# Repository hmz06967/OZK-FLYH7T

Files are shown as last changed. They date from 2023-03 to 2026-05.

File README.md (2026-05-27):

# OZK-FLYH7T
Eagle design witdh STM32H750x BGA flycontroller board support arduplot and betaflight tested OK but R12 no connect Vbat and can be add to boot button Just has a TP and Vbus not connected to +5V.

## Ekran Görüntüleri

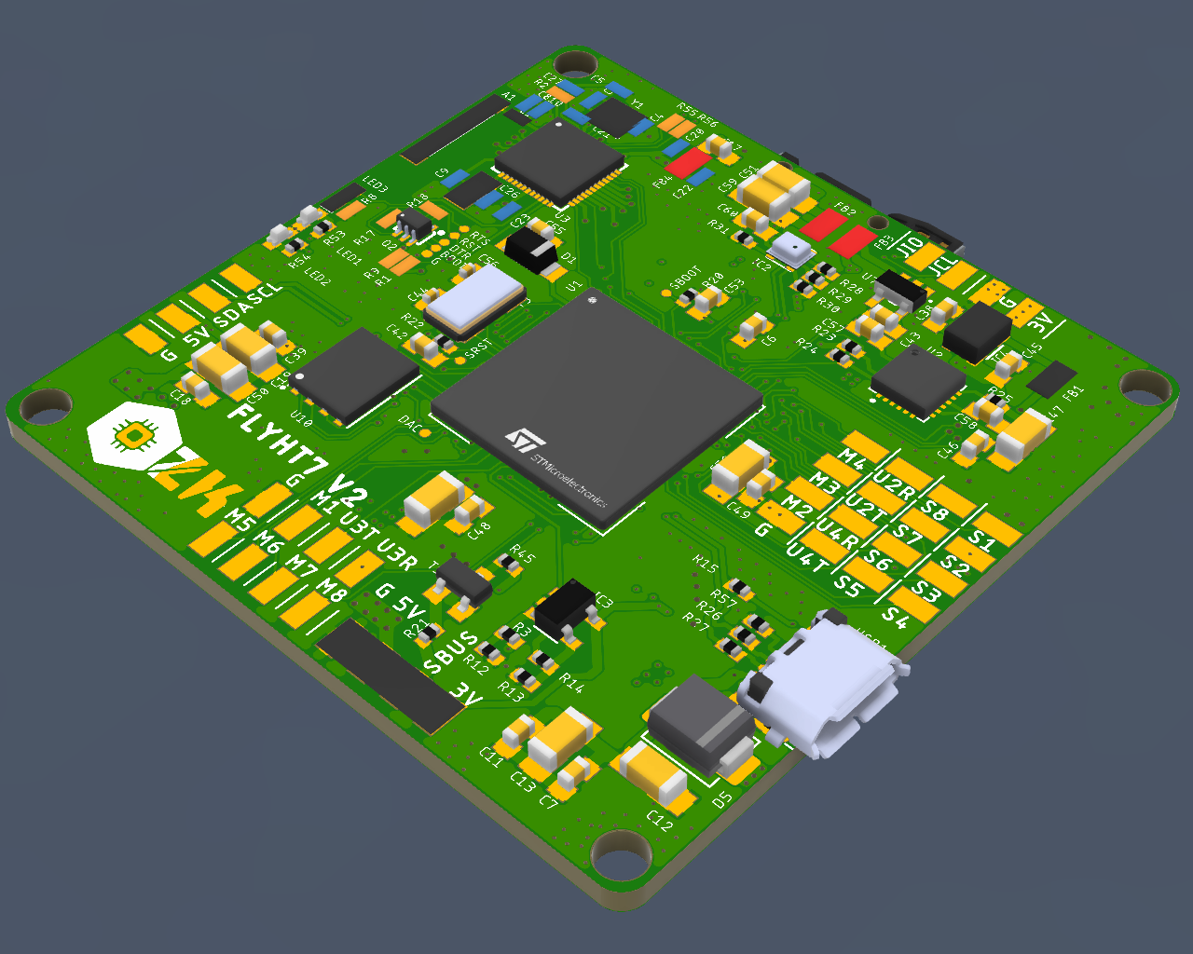
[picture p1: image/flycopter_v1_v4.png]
Uygulama Logo Görüntüsü


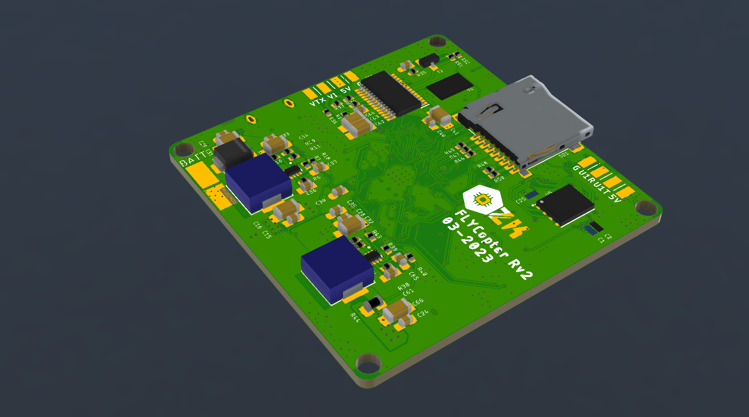
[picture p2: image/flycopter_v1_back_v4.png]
Uygulama Ekran Görüntüsü


[Canlı yazılım testi](https://www.youtube.com/watch?v=nz5CqahaaQQ)

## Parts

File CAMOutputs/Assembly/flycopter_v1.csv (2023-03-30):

Qty | Value | Device | Package | Parts | Description | ARROW_PART_NUMBER | ARROW_PRICE-STOCK | AVAILABILITY | CATEGORY | CREATED_BY | DESCRIPTION | DIGIKEY_PART_NUMBER | HEIGHT | MANUFACTURER | MANUFACTURER_NAME | MANUFACTURER_PART_NUMBER | MF | MOUSER_PART_NUMBER | MOUSER_PRICE-STOCK | MP | MPN | OPERATING_TEMP | PACKAGE | PART_STATUS | POPULARITY | PRICE | PROD_ID | PURCHASE-URL | ROHS_COMPLIANT | SERIES | SPICEPREFIX | SUB-CATEGORY | THERMALLOSS | TP_SIGNAL_NAME | TYPE | VALUE
1 |  | ANTENNA2.4GHZ-8.0X1.0MM | ANT-2.4GHZ-8.0X1.0MM | A1 | Single-ended Antennae |  |  |  |  |  |  |  |  |  |  |  |  |  |  |  |  |  |  |  |  |  | ANT-14377
1 |  | SMD5 | SMD2,54-5,08 | BATT | SMD PAD |  |  |  |  |  |  |  |  |  |  |  |  |  |  |  |  |  |  |  | 21
1 | 0 | 0OHM-0402T-1/10W | 0402-TIGHT | L1 | 0Ω resistor |  |  |  |  |  |  |  |  |  |  |  |  |  |  |  |  |  |  |  |  |  | RES-14244 |  |  |  |  |  |  |  |  | 0
2 | 0 | 10KOHM-0402T-1/16W-1% | 0402-TIGHT | R55, R56 | 10kΩ resistor |  |  |  |  |  |  |  |  |  |  |  |  |  |  |  |  |  |  |  |  |  | RES-14241 |  |  |  |  |  |  |  |  | 10k
1 | 0 | R-US_M0805 | M0805 | R44 | RESISTOR, American symbol |  |  |  |  |  |  |  |  |  |  |  |  |  |  |  |  |  |  |  | 45 |  |  |  |  |  | R
5 | 0 | R-US_R0402 | R0402 | R6, R11, R14, R38, R41 | RESISTOR, American symbol |  |  |  |  |  |  |  |  |  |  |  |  |  |  |  |  |  |  |  | 34 |  |  |  |  |  | R
4 | 0.1uF | 0.1UF-0402T-16V-10% | 0402-TIGHT | C20, C21, C23, C25 | 0.1µF ceramic capacitors |  |  |  |  |  |  |  |  |  |  |  |  |  |  |  |  |  |  |  |  |  | CAP-12416 |  |  |  |  |  |  |  |  | 0.1uF
3 | 100k | R-US_R0402 | R0402 | R10, R20, R22 | RESISTOR, American symbol |  |  |  |  |  |  |  |  |  |  |  |  |  |  |  |  |  |  |  | 34 |  |  |  |  |  | R
27 | 100nF | C-EUC0603K | C0603K | C7, C11, C14, C15, C17, C18, C24, C28, C29, C33, C35, C36, C39, C40, C42, C43, C45, C46, C48, C49, C53, C55, C57, C58, C60, C61, C64 | CAPACITOR, European symbol |  |  |  |  |  |  |  |  |  |  |  |  |  |  |  |  |  |  |  | 30 |  |  |  |  |  | C
1 | 100uF | CPOL-EUA/3216-18R | A/3216-18R | C62 | POLARIZED CAPACITOR, European symbol
1 | 10118193-0001LF | MICRO-USB-SMD-B-(10118193-0001LF) | MICRO-USB5+6P-SMD-0.65-B | USB1 | Seeed SKU 320010003 - SMD Micro USB-B |  |  |  |  |  |  |  |  |  |  |  |  |  |  |  | 10118193-0001LF |  |  |  |  |  |  |  |  |  |  |  |  |  |  | 10118193-0001LF
4 | 10k | 10KOHM-0402T-1/16W-1% | 0402-TIGHT | R1, R9, R17, R18 | 10kΩ resistor |  |  |  |  |  |  |  |  |  |  |  |  |  |  |  |  |  |  |  |  |  | RES-14241 |  |  |  |  |  |  |  |  | 10k
13 | 10k | R-US_R0402 | R0402 | R7, R32, R33, R34, R35, R39, R45, R46, R47, R48, R49, R50, R51 | RESISTOR, American symbol |  |  |  |  |  |  |  |  |  |  |  |  |  |  |  |  |  |  |  | 34 |  |  |  |  |  | R
1 | 10nF | 10NF-0402T-25V-10% | 0402-TIGHT | C5 | 0.01uF/10nF/10,000pF ceramic capacitors |  |  |  |  |  |  |  |  |  |  |  |  |  |  |  |  |  |  |  |  |  | CAP-14847 |  |  |  |  |  |  |  |  | 10nF
1 | 10nF | C-EUC0603K | C0603K | C38 | CAPACITOR, European symbol |  |  |  |  |  |  |  |  |  |  |  |  |  |  |  |  |  |  |  | 30 |  |  |  |  |  | C
1 | 10uF | 10UF-0402T-6.3V-20% | 0402-TIGHT | C22 | 10.0µF ceramic capacitors |  |  |  |  |  |  |  |  |  |  |  |  |  |  |  |  |  |  |  |  |  | CAP-14848 |  |  |  |  |  |  |  |  | 10uF
2 | 12pF | 12PF-0402T-50V-5% | 0402-TIGHT | C3, C4 | 12pF ceramic capacitors |  |  |  |  |  |  |  |  |  |  |  |  |  |  |  |  |  |  |  |  |  | CAP-14665 |  |  |  |  |  |  |  |  | 12pF
2 | 15pF | 15PF-0402T-50V-5% | 0402-TIGHT | C9, C26 | 15pF ceramic capacitors |  |  |  |  |  |  |  |  |  |  |  |  |  |  |  |  |  |  |  |  |  | CAP-13063 |  |  |  |  |  |  |  |  | 15pF
1 | 1M | R-US_R0402 | R0402 | R13 | RESISTOR, American symbol |  |  |  |  |  |  |  |  |  |  |  |  |  |  |  |  |  |  |  | 34 |  |  |  |  |  | R
11 | 1X4SMT | 1X4SMT | 1X4-SMT | CN1, CN2, CN3, CN4, CN5, CN6, CN7, CN8, CN9, CN10, CN11 | 4-pin connector
1 | 1k | 1KOHM-0402T-1/16W-1% | 0402-TIGHT | R8 | 1kΩ resistor |  |  |  |  |  |  |  |  |  |  |  |  |  |  |  |  |  |  |  |  |  | RES-14342 |  |  |  |  |  |  |  |  | 1k
1 | 1k | R-US_R0402 | R0402 | R21 | RESISTOR, American symbol |  |  |  |  |  |  |  |  |  |  |  |  |  |  |  |  |  |  |  | 34 |  |  |  |  |  | R
8 | 2.2k | R-US_R0402 | R0402 | R23, R24, R25, R28, R29, R30, R31, R52 | RESISTOR, American symbol |  |  |  |  |  |  |  |  |  |  |  |  |  |  |  |  |  |  |  | 34 |  |  |  |  |  | R
2 | 2.2uF | C-EUC0603K | C0603K | C6, C30 | CAPACITOR, European symbol |  |  |  |  |  |  |  |  |  |  |  |  |  |  |  |  |  |  |  | 30 |  |  |  |  |  | C
1 | 20k | 20KOHM-0402T-1/16W-1% | 0402-TIGHT | R2 | 20kΩ resistor |  |  |  |  |  |  |  |  |  |  |  |  |  |  |  |  |  |  |  |  |  | RES-15131 |  |  |  |  |  |  |  |  | 20k
2 | 22 | R-US_R0402 | R0402 | R26, R27 | RESISTOR, American symbol |  |  |  |  |  |  |  |  |  |  |  |  |  |  |  |  |  |  |  | 34 |  |  |  |  |  | R
2 | 22pF | C-EUC0402K | C0402K | C44, C56 | CAPACITOR, European symbol |  |  |  |  |  |  |  |  |  |  |  |  |  |  |  |  |  |  |  | 15 |  |  |  |  |  | C
1 | 22uF | CPOL-EUA/3216-18R | A/3216-18R | C63 | POLARIZED CAPACITOR, European symbol
3 | 270k | R-US_R0402 | R0402 | R3, R16, R42 | RESISTOR, American symbol |  |  |  |  |  |  |  |  |  |  |  |  |  |  |  |  |  |  |  | 34 |  |  |  |  |  | R
2 | 270pF | 270PF-0402T-50V-5% | 0402-TIGHT | C1, C2 | 270pF/0.27nF ceramic capacitors |  |  |  |  |  |  |  |  |  |  |  |  |  |  |  |  |  |  |  |  |  | CAP-15129 |  |  |  |  |  |  |  |  | 270pF
1 | 27k | R-US_R0402 | R0402 | R12 | RESISTOR, American symbol |  |  |  |  |  |  |  |  |  |  |  |  |  |  |  |  |  |  |  | 34 |  |  |  |  |  | R
1 | 3.0nF | 3.0NF-0402T-50V-5% | 0402-TIGHT | C27 | 3.0nF (3nF, 3000pF) ceramic capacitors |  |  |  |  |  |  |  |  |  |  |  |  |  |  |  |  |  |  |  |  |  | CAP-15130 |  |  |  |  |  |  |  |  | 3.0nF
1 | 3.3V | V_REG_AP2112K-3.3V | SOT23-5 | U7 | AP2112 - 600mA CMOS LDO Regulator w/ Enable |  |  |  |  |  |  |  |  |  |  |  |  |  |  |  |  |  |  |  |  |  | VREG-12457 |  |  |  |  |  |  |  |  | 3.3V
1 | 32.768kHz | CRYSTAL-32.768KHZSMD-3.2X1.5 | CRYSTAL-SMD-3.2X1.5MM | Y2 | 32.768kHz Crystal |  |  |  |  |  |  |  |  |  |  |  |  |  |  |  |  |  |  |  |  |  | XTAL-13062 |  |  |  |  |  |  |  |  | 32.768kHz
2 | 330 | R-US_R0402 | R0402 | R53, R54 | RESISTOR, American symbol |  |  |  |  |  |  |  |  |  |  |  |  |  |  |  |  |  |  |  | 34 |  |  |  |  |  | R
2 | 33nF | C-EUC0603K | C0603K | C37, C65 | CAPACITOR, European symbol |  |  |  |  |  |  |  |  |  |  |  |  |  |  |  |  |  |  |  | 30 |  |  |  |  |  | C
1 | 4.7k | R-US_R0402 | R0402 | R15 | RESISTOR, American symbol |  |  |  |  |  |  |  |  |  |  |  |  |  |  |  |  |  |  |  | 34 |  |  |  |  |  | R
1 | 4.7uH | 0630CDMCCDS-4R7MC | 0630CDMCCDS-4R7MC | U$9 | Check availability |  |  | In Stock |  |  | 4.7 µH Shielded Molded Inductor 6.3 A 33mOhm Max Nonstandard |  |  |  |  |  | Sumida |  |  | 0630CDMCCDS-4R7MC |  |  | Nonstandard Sumida |  |  | None |  | https://pricing.snapeda.com/search/part/0630CDMCCDS-4R7MC/?ref=eda
1 | 40MHz | CRYSTAL-40MHZ-SMD-2X2.5MM | CRYSTAL-SMD-2X2.5MM | Y1 | 40MHz Crystal w/ Ground Pin |  |  |  |  |  |  |  |  |  |  |  |  |  |  |  |  |  |  |  |  |  | XTAL-15127 |  |  |  |  |  |  |  |  | 40MHZ
15 | 47uF | CPOL-EUA/3216-18R | A/3216-18R | C12, C13, C16, C19, C31, C32, C34, C41, C47, C50, C51, C52, C54, C59, C66 | POLARIZED CAPACITOR, European symbol
1 | 5.11k | R-US_R0402 | R0402 | R57 | RESISTOR, American symbol |  |  |  |  |  |  |  |  |  |  |  |  |  |  |  |  |  |  |  | 34 |  |  |  |  |  | R
2 | 50k | R-US_R0402 | R0402 | R19, R43 | RESISTOR, American symbol |  |  |  |  |  |  |  |  |  |  |  |  |  |  |  |  |  |  |  | 34 |  |  |  |  |  | R
1 | 6.8uH | 0630CDMCCDS-4R7MC | 0630CDMCCDS-4R7MC | U$5 | Check availability |  |  | In Stock |  |  | 4.7 µH Shielded Molded Inductor 6.3 A 33mOhm Max Nonstandard |  |  |  |  |  | Sumida |  |  | 0630CDMCCDS-4R7MC |  |  | Nonstandard Sumida |  |  | None |  | https://pricing.snapeda.com/search/part/0630CDMCCDS-4R7MC/?ref=eda
4 | 600Ω | FERRITE_BEAD-0805-600Ω-100MHZ | 0805 | FB1, FB2, FB3, FB4 | Ferrite Bead (blocks, cores, rings, chokes, etc.) |  |  |  |  |  |  |  |  |  |  |  |  |  |  |  |  |  |  |  |  |  | NDUC-14988 |  |  |  |  |  |  |  |  | 600Ω
2 | 75 | R-US_R0402 | R0402 | R36, R37 | RESISTOR, American symbol |  |  |  |  |  |  |  |  |  |  |  |  |  |  |  |  |  |  |  | 34 |  |  |  |  |  | R
1 | 80k | R-US_R0402 | R0402 | R40 | RESISTOR, American symbol |  |  |  |  |  |  |  |  |  |  |  |  |  |  |  |  |  |  |  | 34 |  |  |  |  |  | R
1 | AT7456E | AT7456E | SOP65P640X120-29N | IC1 | Video Character Overlay Chip (OSD) |  |  |  |  |  | Video Character Overlay Chip (OSD) |  | 1.2mm |  | ICOF | AT7456E
1 | BAS16J | DIODE_DIODE-SOD123 | DIODE_SOD123 | D1 | DIODE
2 | BC817C | BC817-16-NPN-SOT23-BEC | SOT23-BEC | T1, T2 | NPN Transistror |  |  |  |  |  |  |  |  |  |  |  |  |  |  |  |  |  |  |  | 0
1 | BLUE | LED-BLUE0603 | LED-0603 | LED3 | Blue SMD LED |  |  |  |  |  |  |  |  |  |  |  |  |  |  |  |  |  |  |  |  |  | DIO-08575 |  |  |  |  |  |  |  |  | BLUE
1 | BMP280 | BMP280 | BMP280 | IC2 | BOSCH BMP280 Digital Pressure Sensor
2 | DNP | CAP-0402-TIGHT | 0402-TIGHT | C8, C10
2 | ECS-240-12-30BQ-AEN-TR | ECS-240-12-30BQ-AEN-TR | XTAL_ECS-240-12-30BQ-AEN-TR | Y3, Y4 | The ECX-53BQ is a miniature SMD Crystal with a 3.2 x 5 mm |  |  | In Stock |  |  | 24 MHz ±25ppm Crystal 12pF 30 Ohms 4-SMD, No Lead |  |  |  |  |  | ECS Inc. |  |  | ECS-240-12-30BQ-AEN-TR |  |  | SMD-4 ECS International |  |  | None |  | https://pricing.snapeda.com/search/part/ECS-240-12-30BQ-AEN-TR/?ref=eda
1 | ESP32 | ESP32 | QFN48-0.4MM | U3 | Espressif ESP32 |  |  |  |  |  |  |  |  |  |  |  |  |  |  |  |  |  |  |  |  |  | IC-13338
1 | LD398518RG | LD398518RG | TSOT23-5L | IC4 | Ultra low drop and low noise BiCMOS voltage regulators |  |  |  |  |  |  |  |  |  |  |  |  |  |  |  |  |  |  |  | 0
1 | MBT3904DW1T1 | TRANS_NPN_DUAL-MBT3904DW1T1 | SC70-6 | Q2 | Dual NPN Transistors in Single Package |  |  |  |  |  |  |  |  |  |  |  |  |  |  |  |  |  |  |  |  |  | TRANS-13337
1 | MCP6001T_SOT23 | MCP6001T_SOT23 | SOT95P280X145-5N | IC3 | Low-Power Operational Amplifier |  |  |  | Amplifier |  | Low-Power Operational Amplifier |  |  | Microchip Technology |  |  |  |  |  |  | Generic |  |  |  |  |  |  |  |  | MCP6001 |  | OpAmp
1 | MPU-6050 | MPU-6050 | 24-VFQFN | U2 | IMU ACCEL/GYRO 3-AXIS I2C 24QFN |  |  |  |  | PCBLayout.com |  | 1428-1007-1-ND |  | TDK InvenSense |  |  |  |  |  |  | MPU-6050 |  | 24-VFQFN
2 | SS54B | SS54B | SMB | D3, D5 | SURFACE MOUNT SCHOTTKY BARRIER RECTIFIERS |  |  |  |  | PCBLayout.com |  |  |  | JCET |  |  |  |  |  |  | SS54B |  | SMB
1 | STM32H750XBH6 | STM32H750XBH6 | IC_STM32H750XBH6 | U1 | Check availability |  |  | In Stock |  |  | ARM® Cortex®-M7 STM32H7 Microcontroller IC 32-Bit Single-Core 480MHz 128KB (128K x 8) FLASH 240+25-TFBGA (14x14) |  |  |  |  |  | STMicroelectronics |  |  | STM32H750XBH6 |  |  | TFBGA-265 STMicroelectronics |  |  | None |  | https://pricing.snapeda.com/search/part/STM32H750XBH6/?ref=eda
1 | TF-HOLDER | TF-HOLDER | TF-PULL | SD1 | TF / Micro SD socket is PUSH-PUSH type, the card can be pushed into and auto locked and pushed out by simply press the card.
2 | TPS62933PDRLR | TPS62933PDRLR | SOFL50P160X60-8N | U4, U6 | Check availability |  |  | In Stock |  |  | Buck Switching Regulator IC Positive Adjustable 0.8V 1 Output 3A SOT-583 |  |  |  |  |  | Texas Instruments |  |  | TPS62933PDRLR |  |  | None |  |  | None |  | https://pricing.snapeda.com/search/part/TPS62933PDRLR/?ref=eda
8 | TPTP06R | TPTP06R | TP06R | BOOT, DAC, DTR, G, RST, RTS, SBOOT, SRST | Test pad
2 | W25QXX128MBIT-6X5-SKINNY_CENTER | W25QXX128MBIT-6X5-SKINNY_CENTER | WSON-8-6X5-SKINNY_CENTERPAD | U5, U10 |  |  |  |  |  |  |  |  |  |  |  |  |  |  |  |  |  |  |  |  |  |  | IC-15107
1 | blue | LEDCHIPLED_0603 | CHIPLED_0603 | LED1 | LED
1 | green | LEDCHIPLED_0603 | CHIPLED_0603 | LED2 | LED

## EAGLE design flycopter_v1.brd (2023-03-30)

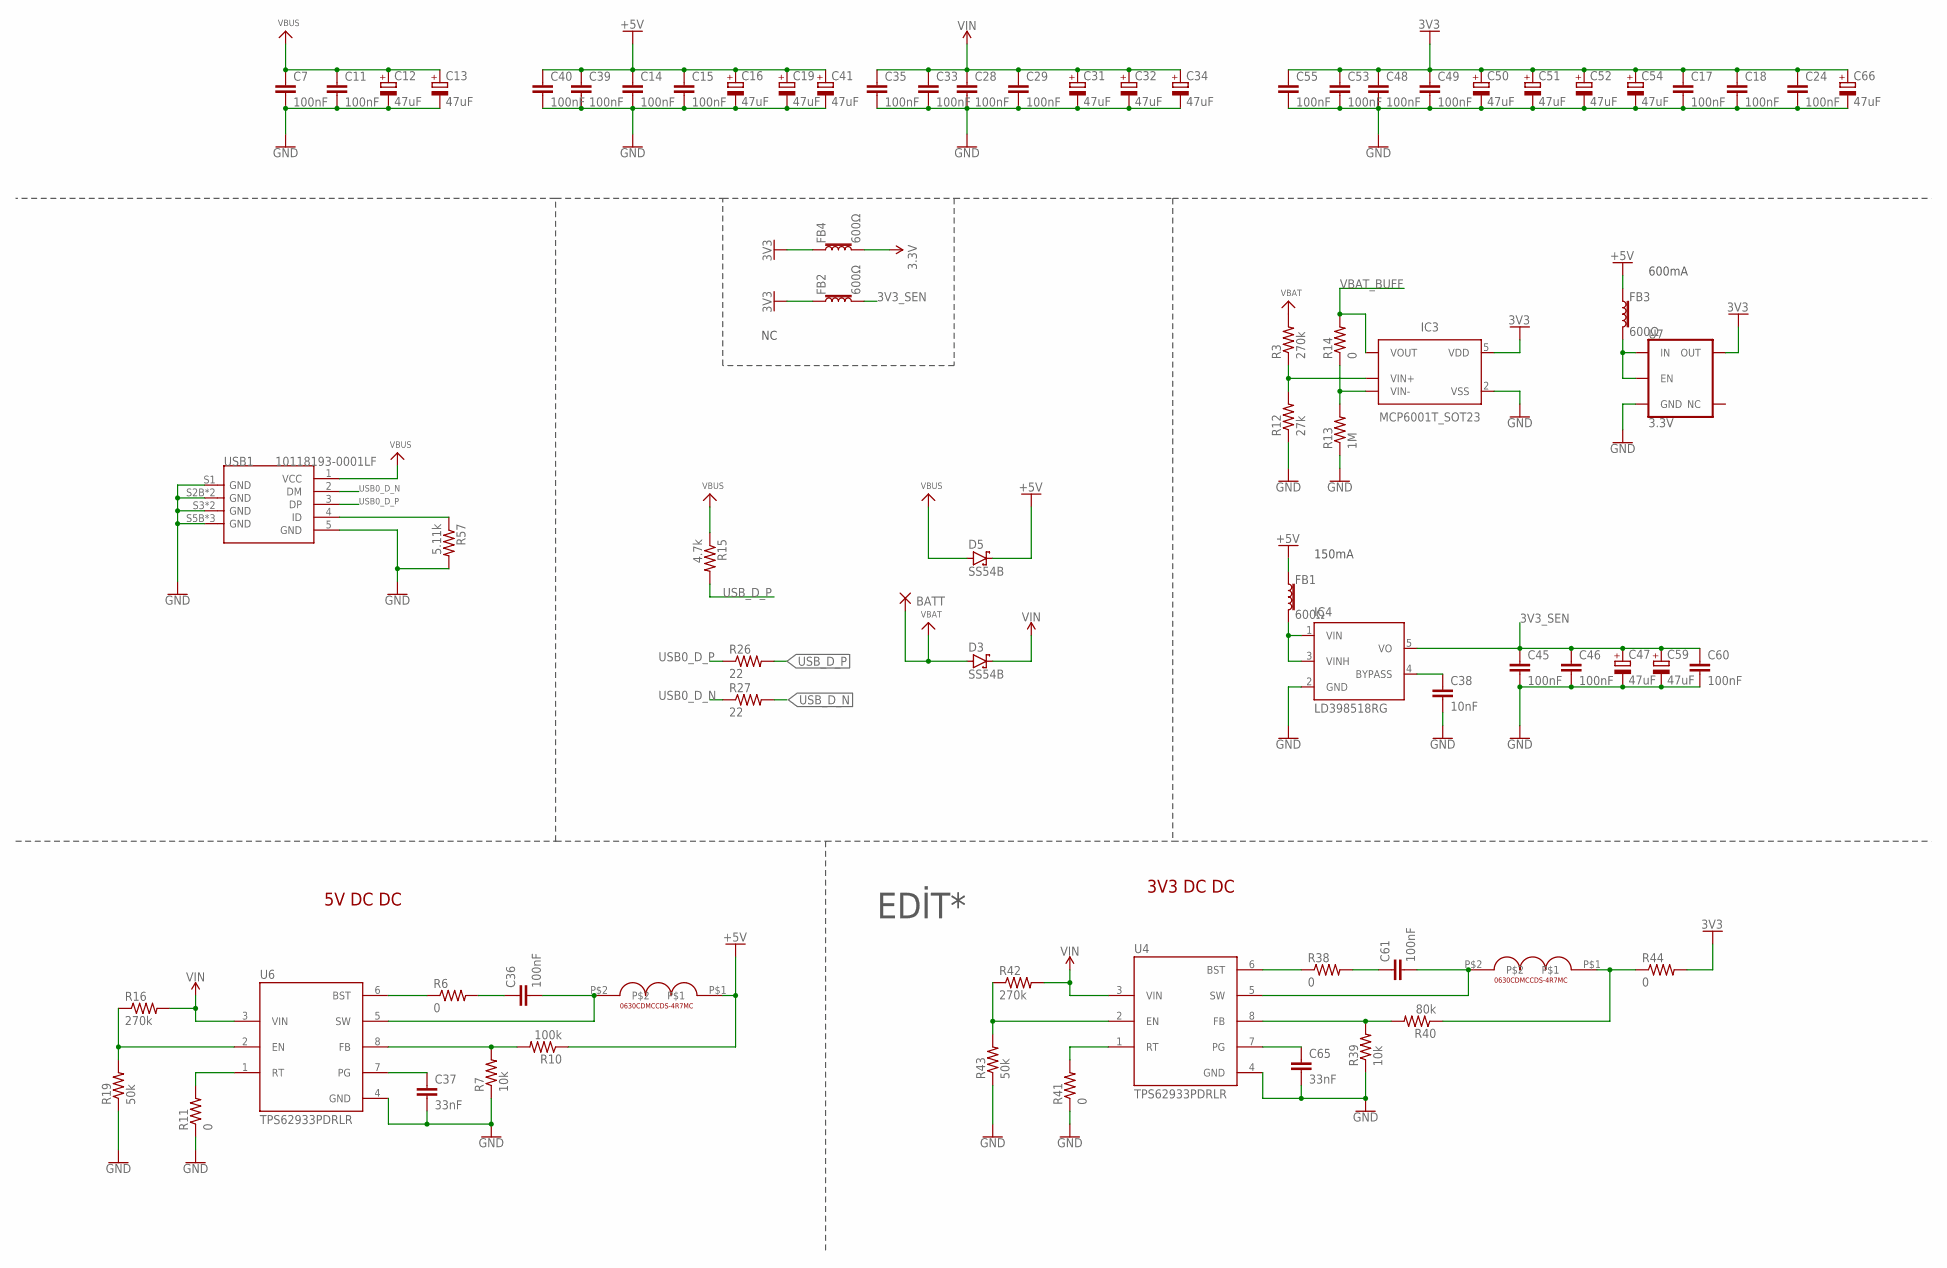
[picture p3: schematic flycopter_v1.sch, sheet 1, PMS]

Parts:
BATT: SMD5; SMD2,54-5,08
C7, C11, C14, C15, C17, C18, C24, C28, C29, C33, C35, C36, C39, C40, C45, C46, C48, C49, C53, C55, C60, C61: 100nF; C0603K
C12, C13, C16, C19, C31, C32, C34, C41, C47, C50, C51, C52, C54, C59, C66: 47uF; A/3216-18R
C37, C65: 33nF; C0603K
C38: 10nF; C0603K
D3, D5: SS54B; SMB
FB1, FB2, FB3, FB4: 600Ω; 0805
IC3: MCP6001T_SOT23; SOT95P280X145-5N
IC4: LD398518RG; TSOT23-5L
R3, R16, R42: 270k; R0402
R6, R11, R14, R38, R41: 0; R0402
R7, R39: 10k; R0402
R10: 100k; R0402
R12: 27k; R0402
R13: 1M; R0402
R15: 4.7k; R0402
R19, R43: 50k; R0402
R26, R27: 22; R0402
R40: 80k; R0402
R44: 0; M0805
R57: 5.11k; R0402
U4, U6: TPS62933PDRLR; SOFL50P160X60-8N
U7: 3.3V; SOT23-5
U$5: 6.8uH; 0630CDMCCDS-4R7MC
U$9: 4.7uH; 0630CDMCCDS-4R7MC
USB1: 10118193-0001LF; MICRO-USB5+6P-SMD-0.65-B

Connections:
3.3V: FB4.2; also elsewhere on the board
3V3: C17.1, C18.1, C24.1, C48.1, C49.1, C50.+, C51.+, C52.+, C53.1, C54.+, C55.1, C66.+, FB2.1, FB4.1, IC3.5 (VDD), R44.2, U7.5 (OUT); also elsewhere on the board
3V3_SEN: C45.1, C46.1, C47.+, C59.+, C60.1, FB2.2, IC4.5 (VO); also elsewhere on the board
+5V: C14.1, C15.1, C16.+, C19.+, C39.1, C40.1, C41.+, D5.C, FB1.1, FB3.1, R10.1, U$5.P$1; also elsewhere on the board
GND: C7.2, C11.2, C12.-, C13.-, C14.2, C15.2, C16.-, C17.2, C18.2, C19.-, C24.2, C28.2, C29.2, C31.-, C32.-, C33.2, C34.-, C35.2, C37.2, C38.2, C39.2, C40.2, C41.-, C45.2, C46.2, C47.-, C48.2, C49.2, C50.-, C51.-, C52.-, C53.2, C54.-, C55.2, C59.-, C60.2, C65.2, C66.-, IC3.2 (VSS), IC4.2 (GND), R7.1, R11.1, R12.1, R13.1, R19.1, R39.1, R41.1, R43.1, R57.2, U4.4 (GND), U6.4 (GND), U7.2 (GND), USB1.5 (GND), USB1.S1 (GND), USB1.S2B (GND), USB1.S2T (GND), USB1.S3 (GND), USB1.S4 (GND), USB1.S5B (GND), USB1.S5T (GND), USB1.S6 (GND); also elsewhere on the board
unnamed: C36.2, U6.5 (SW), U$5.P$2
unnamed: C36.1, R6.2
unnamed: R6.1, U6.6 (BST)
unnamed: R7.2, R10.2, U6.8 (FB)
unnamed: C37.1, U6.7 (PG)
unnamed: R16.1, R19.2, U6.2 (EN)
unnamed: R11.2, U6.1 (RT)
unnamed: FB1.2, IC4.1 (VIN), IC4.3 (VINH)
unnamed: C38.1, IC4.4 (BYPASS)
unnamed: FB3.2, U7.1 (IN), U7.3 (EN)
unnamed: IC3.4 (VIN-), R13.2, R14.1
unnamed: IC3.3 (VIN+), R3.1, R12.2
unnamed: C61.2, U4.5 (SW), U$9.P$2
unnamed: R57.1, USB1.4 (ID)
unnamed: C61.1, R38.2
unnamed: R38.1, U4.6 (BST)
unnamed: R39.2, R40.2, U4.8 (FB)
unnamed: C65.1, U4.7 (PG)
unnamed: R41.2, U4.1 (RT)
unnamed: R42.1, R43.2, U4.2 (EN)
unnamed: R40.1, R44.1, U$9.P$1
USB0_D_N: R27.1, USB1.2 (DM)
USB0_D_P: R26.1, USB1.3 (DP)
USB_D_N: R27.2; also elsewhere on the board
USB_D_P: R15.2, R26.2; also elsewhere on the board
VBAT: BATT.1, D3.A, R3.2
VBAT_BUFF: IC3.1 (VOUT), R14.2; also elsewhere on the board
VBUS: C7.1, C11.1, C12.+, C13.+, D5.A, R15.1, USB1.1 (VCC)
VIN: C28.1, C29.1, C31.+, C32.+, C33.1, C34.+, C35.1, D3.C, R16.2, R42.2, U4.3 (VIN), U6.3 (VIN)

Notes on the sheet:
150mA
600mA
EDİT*
5V DC DC
3V3 DC DC

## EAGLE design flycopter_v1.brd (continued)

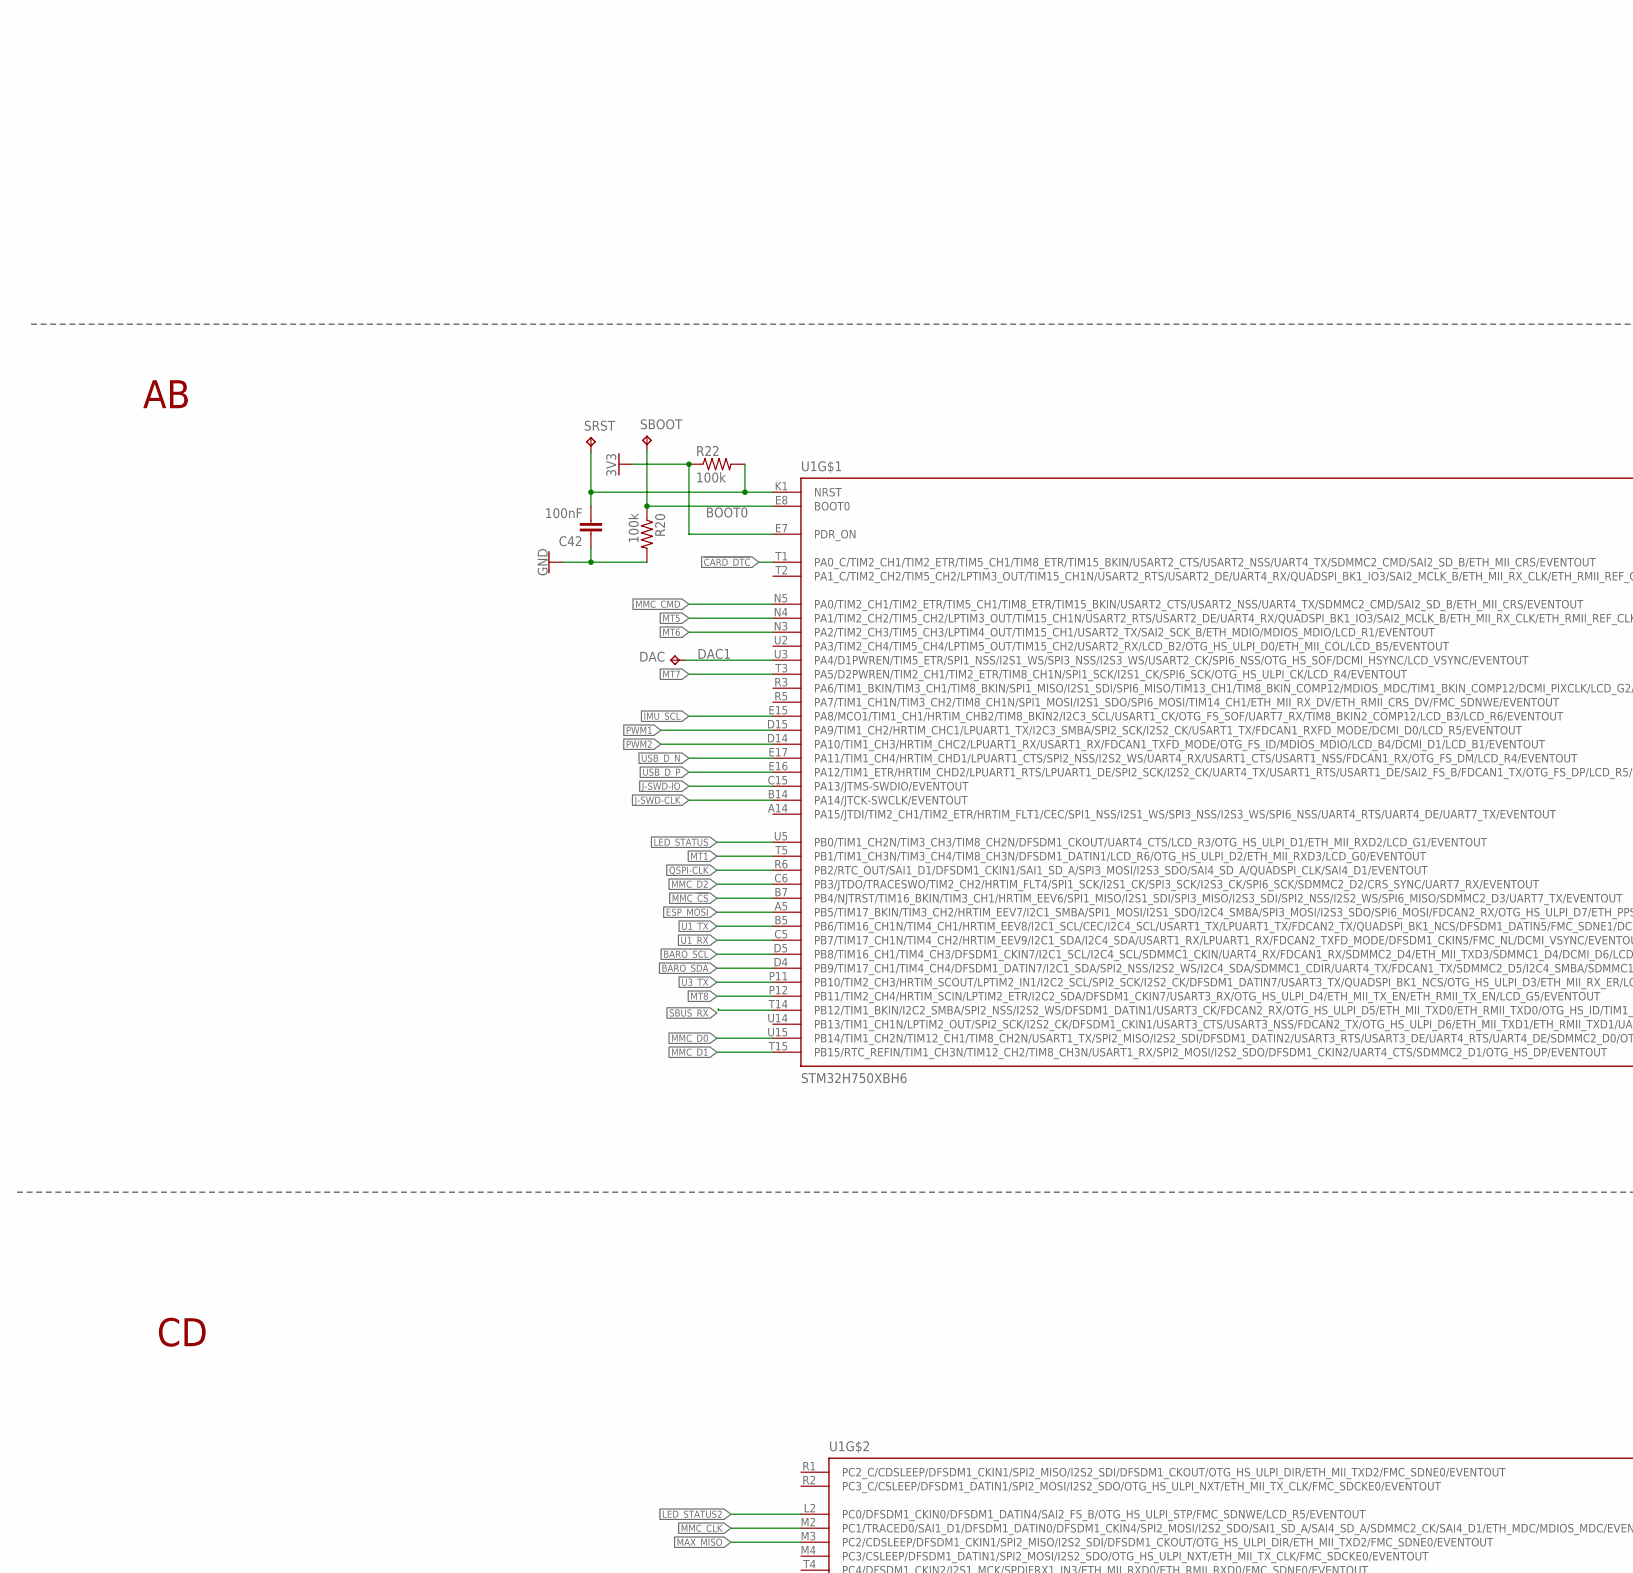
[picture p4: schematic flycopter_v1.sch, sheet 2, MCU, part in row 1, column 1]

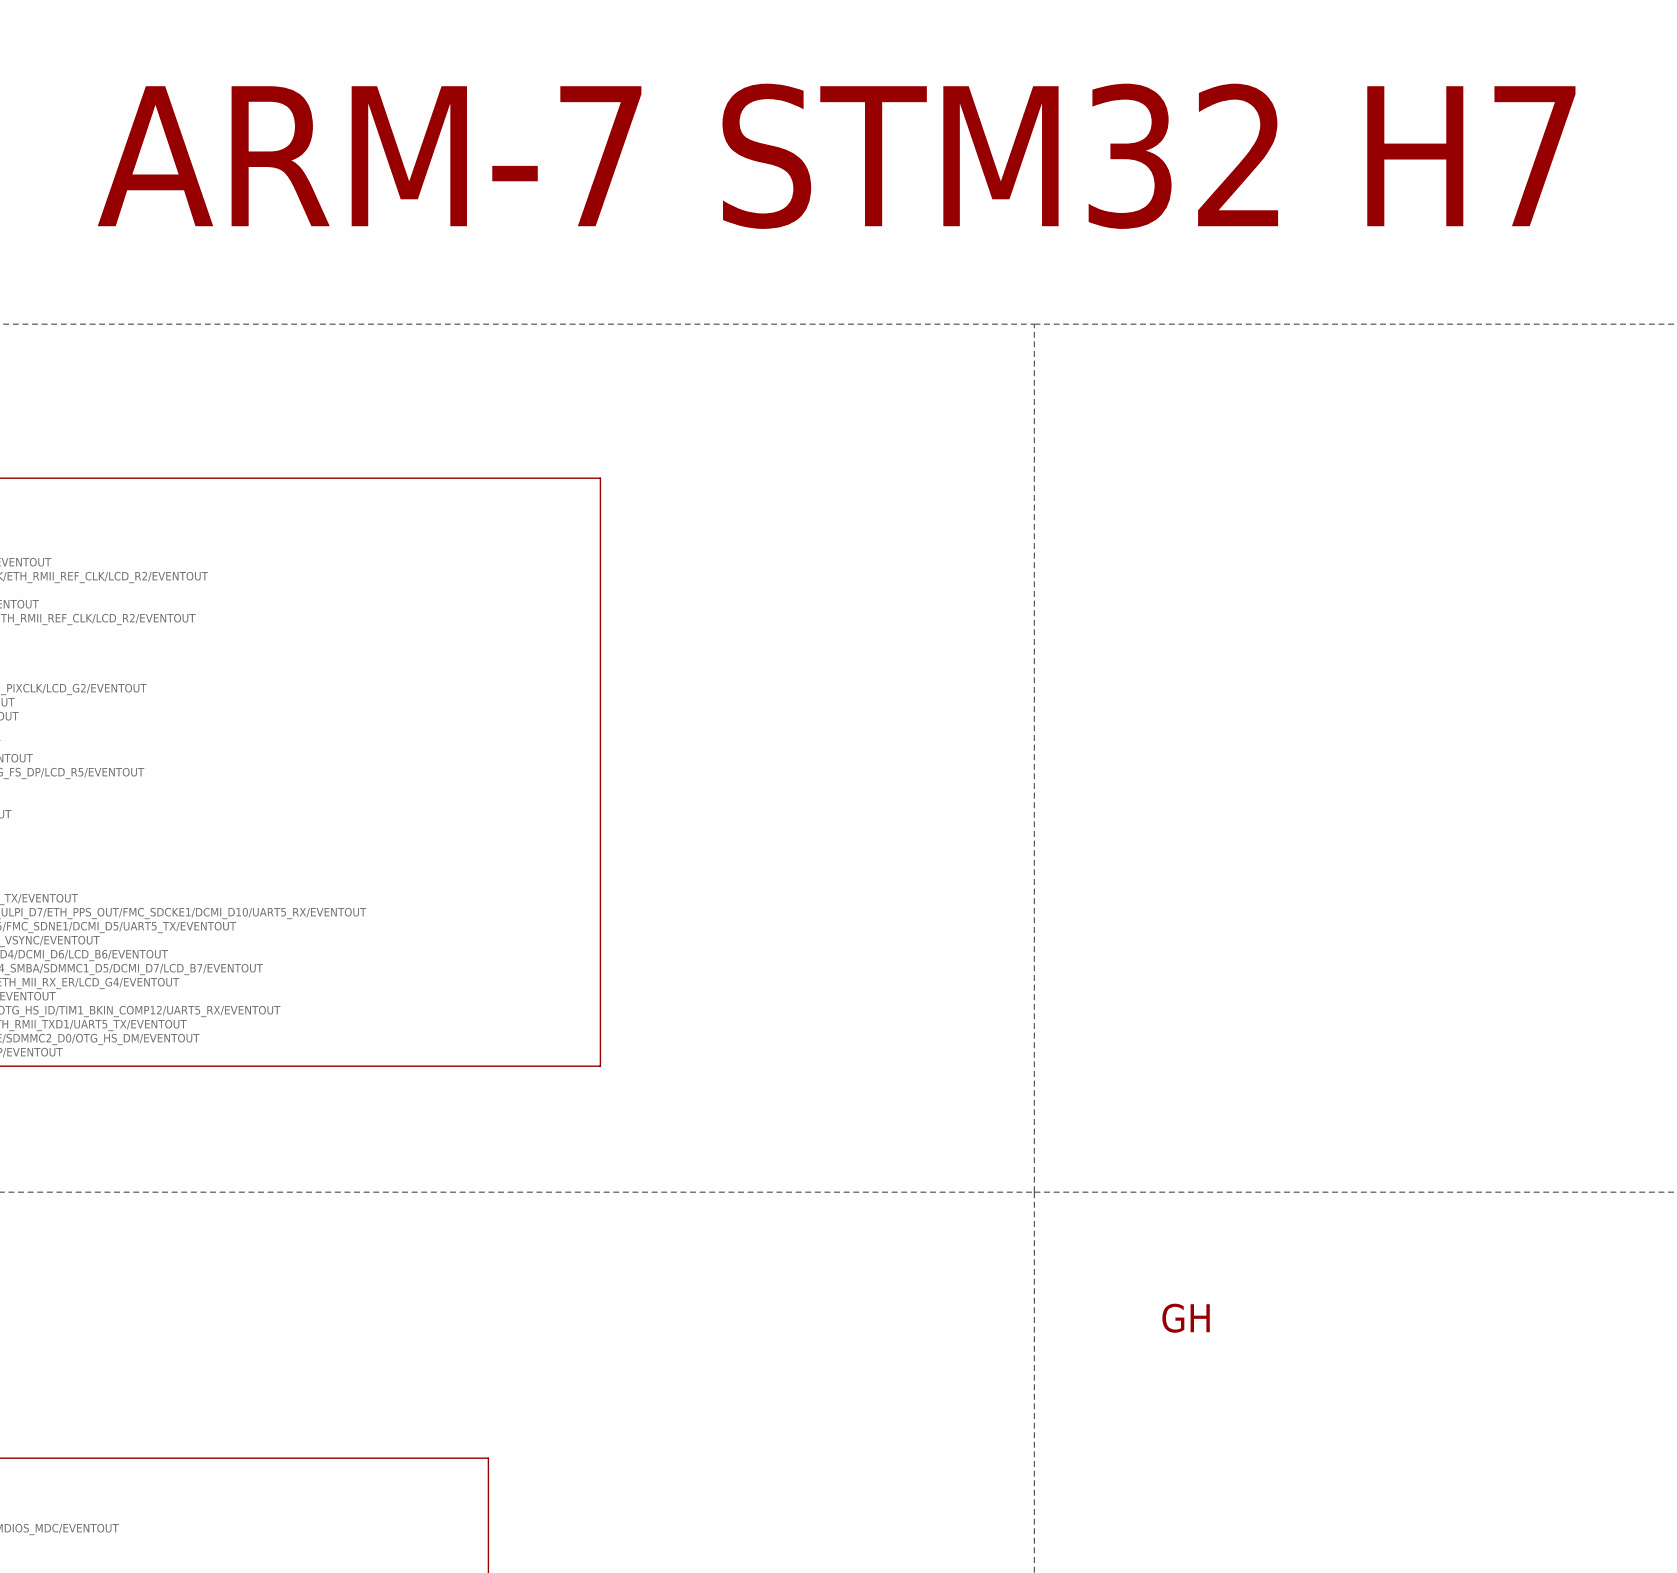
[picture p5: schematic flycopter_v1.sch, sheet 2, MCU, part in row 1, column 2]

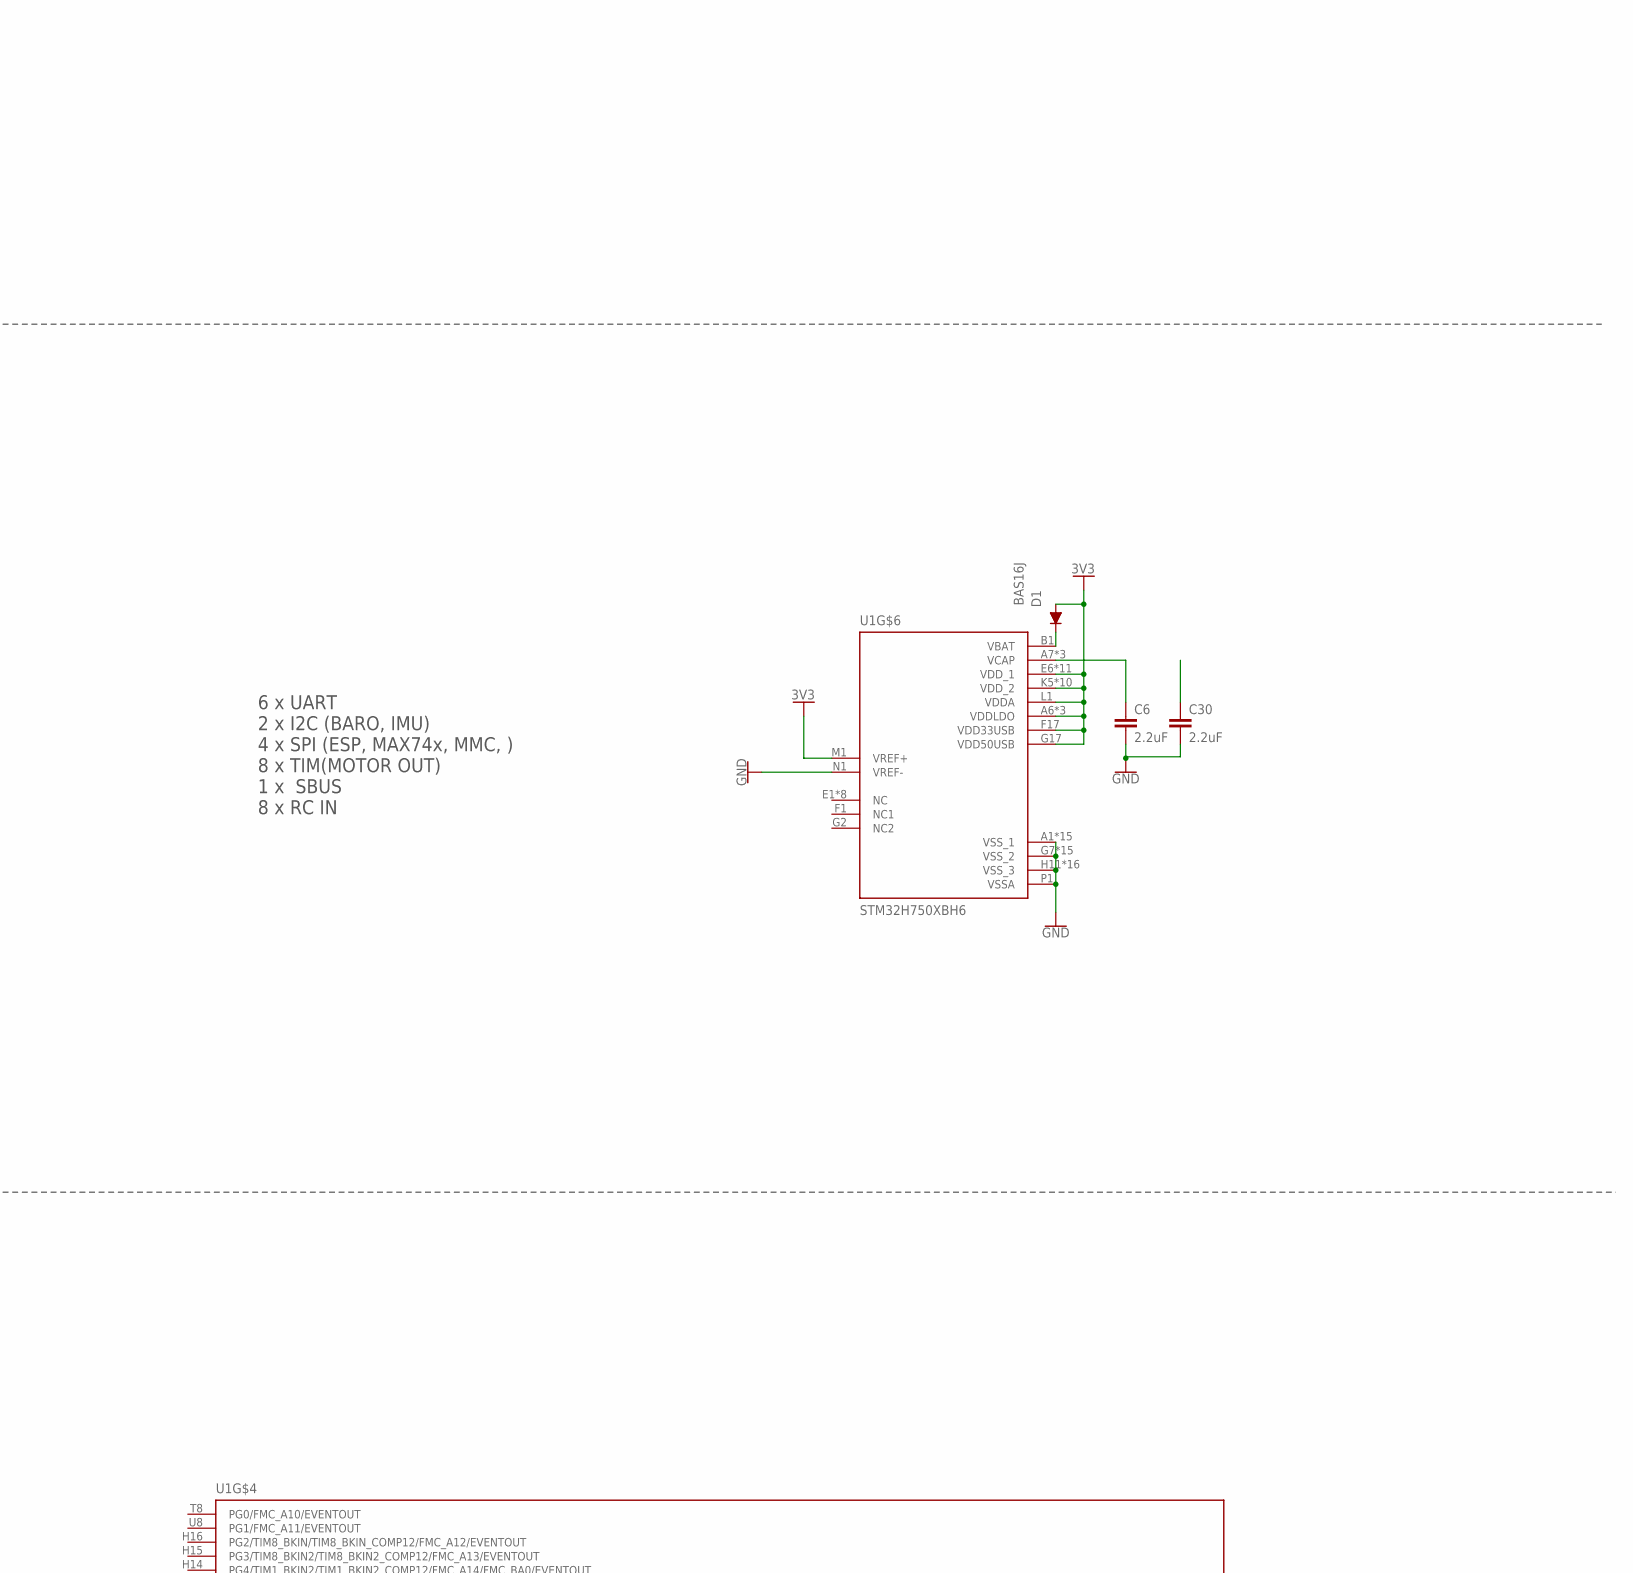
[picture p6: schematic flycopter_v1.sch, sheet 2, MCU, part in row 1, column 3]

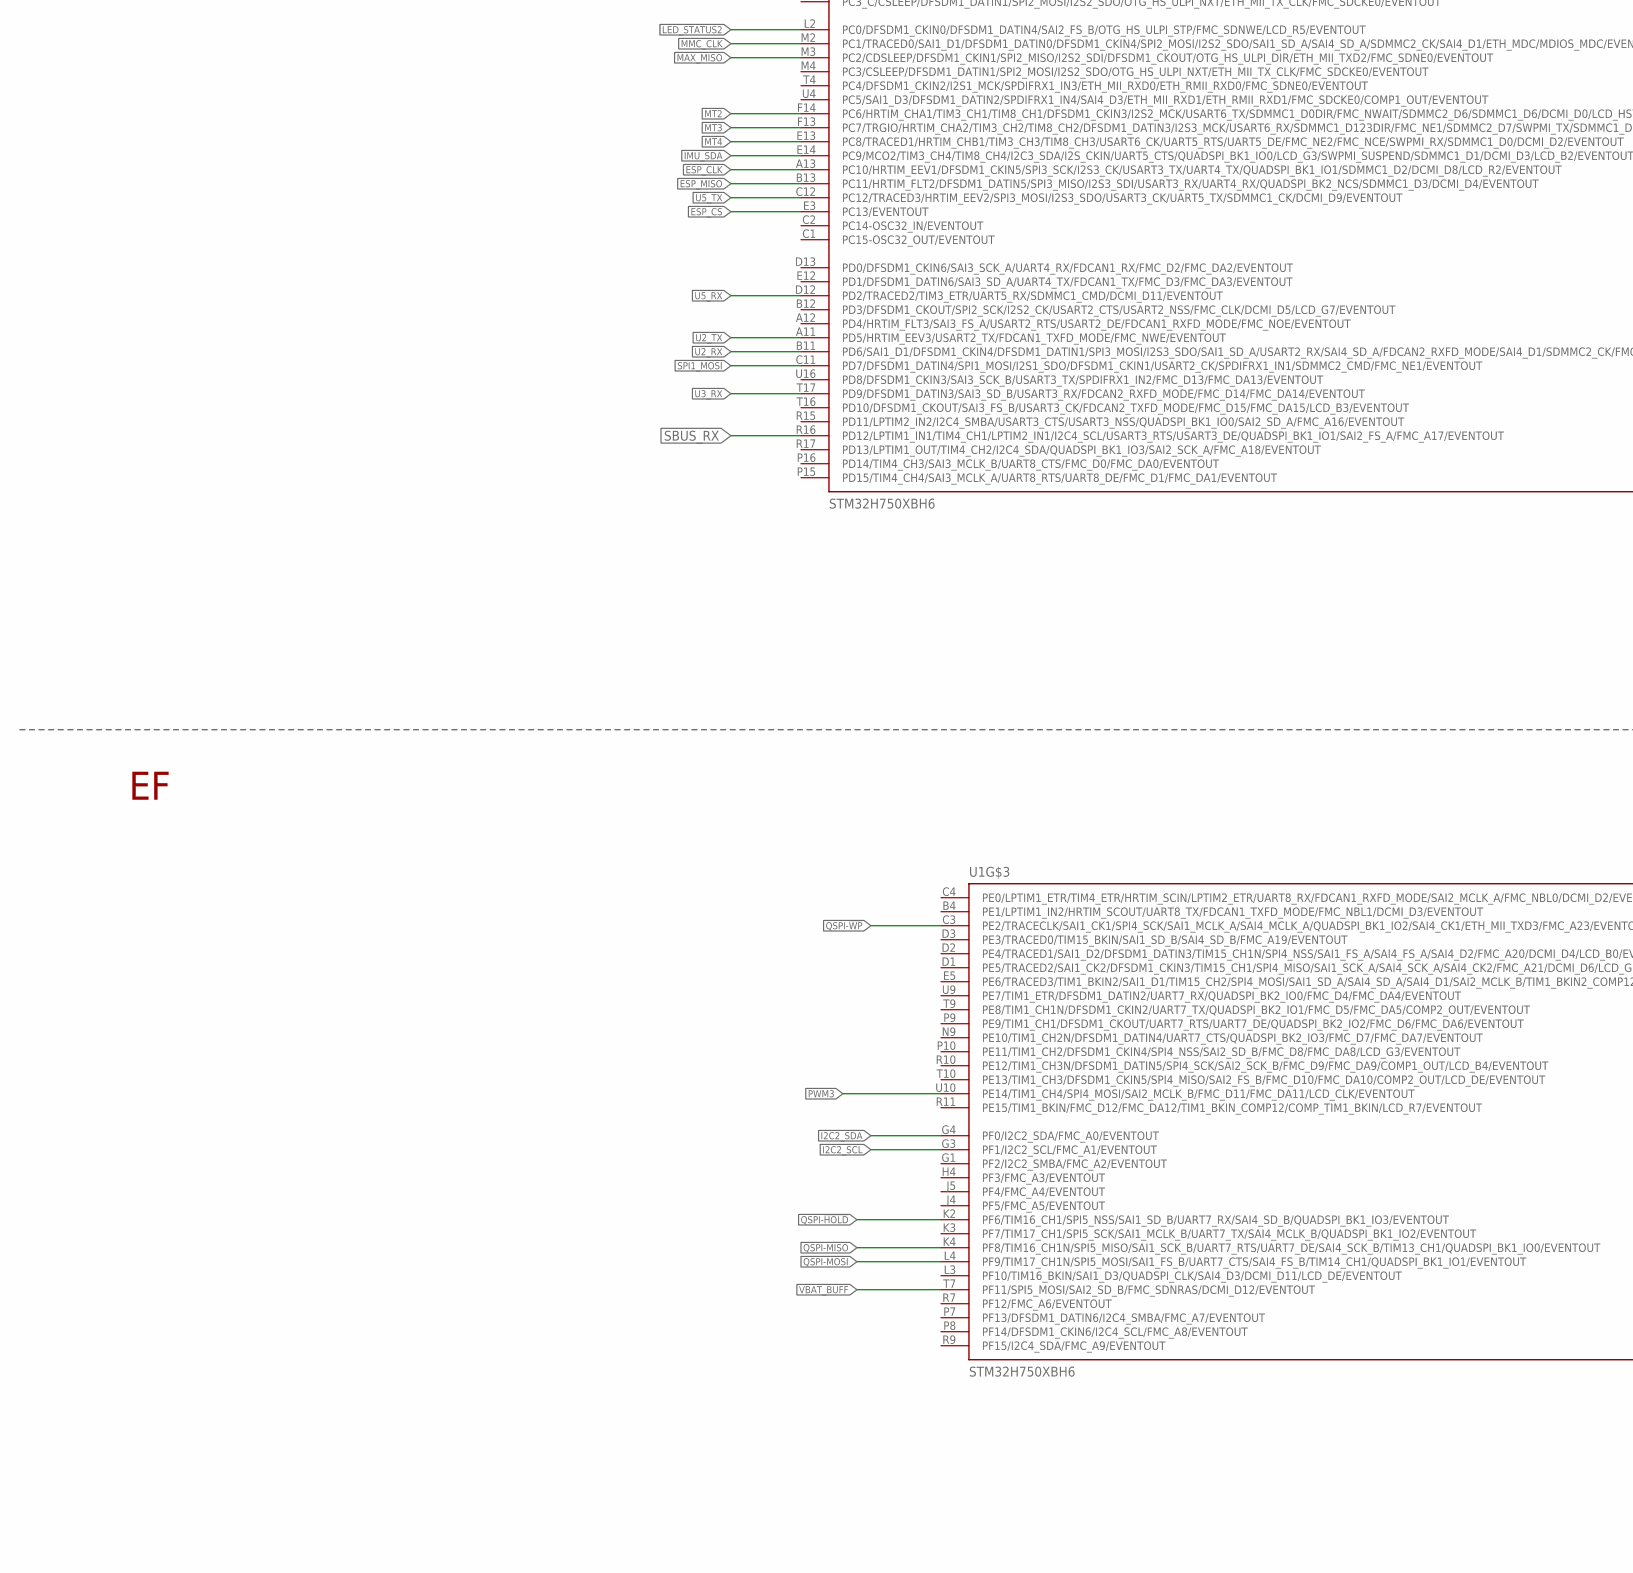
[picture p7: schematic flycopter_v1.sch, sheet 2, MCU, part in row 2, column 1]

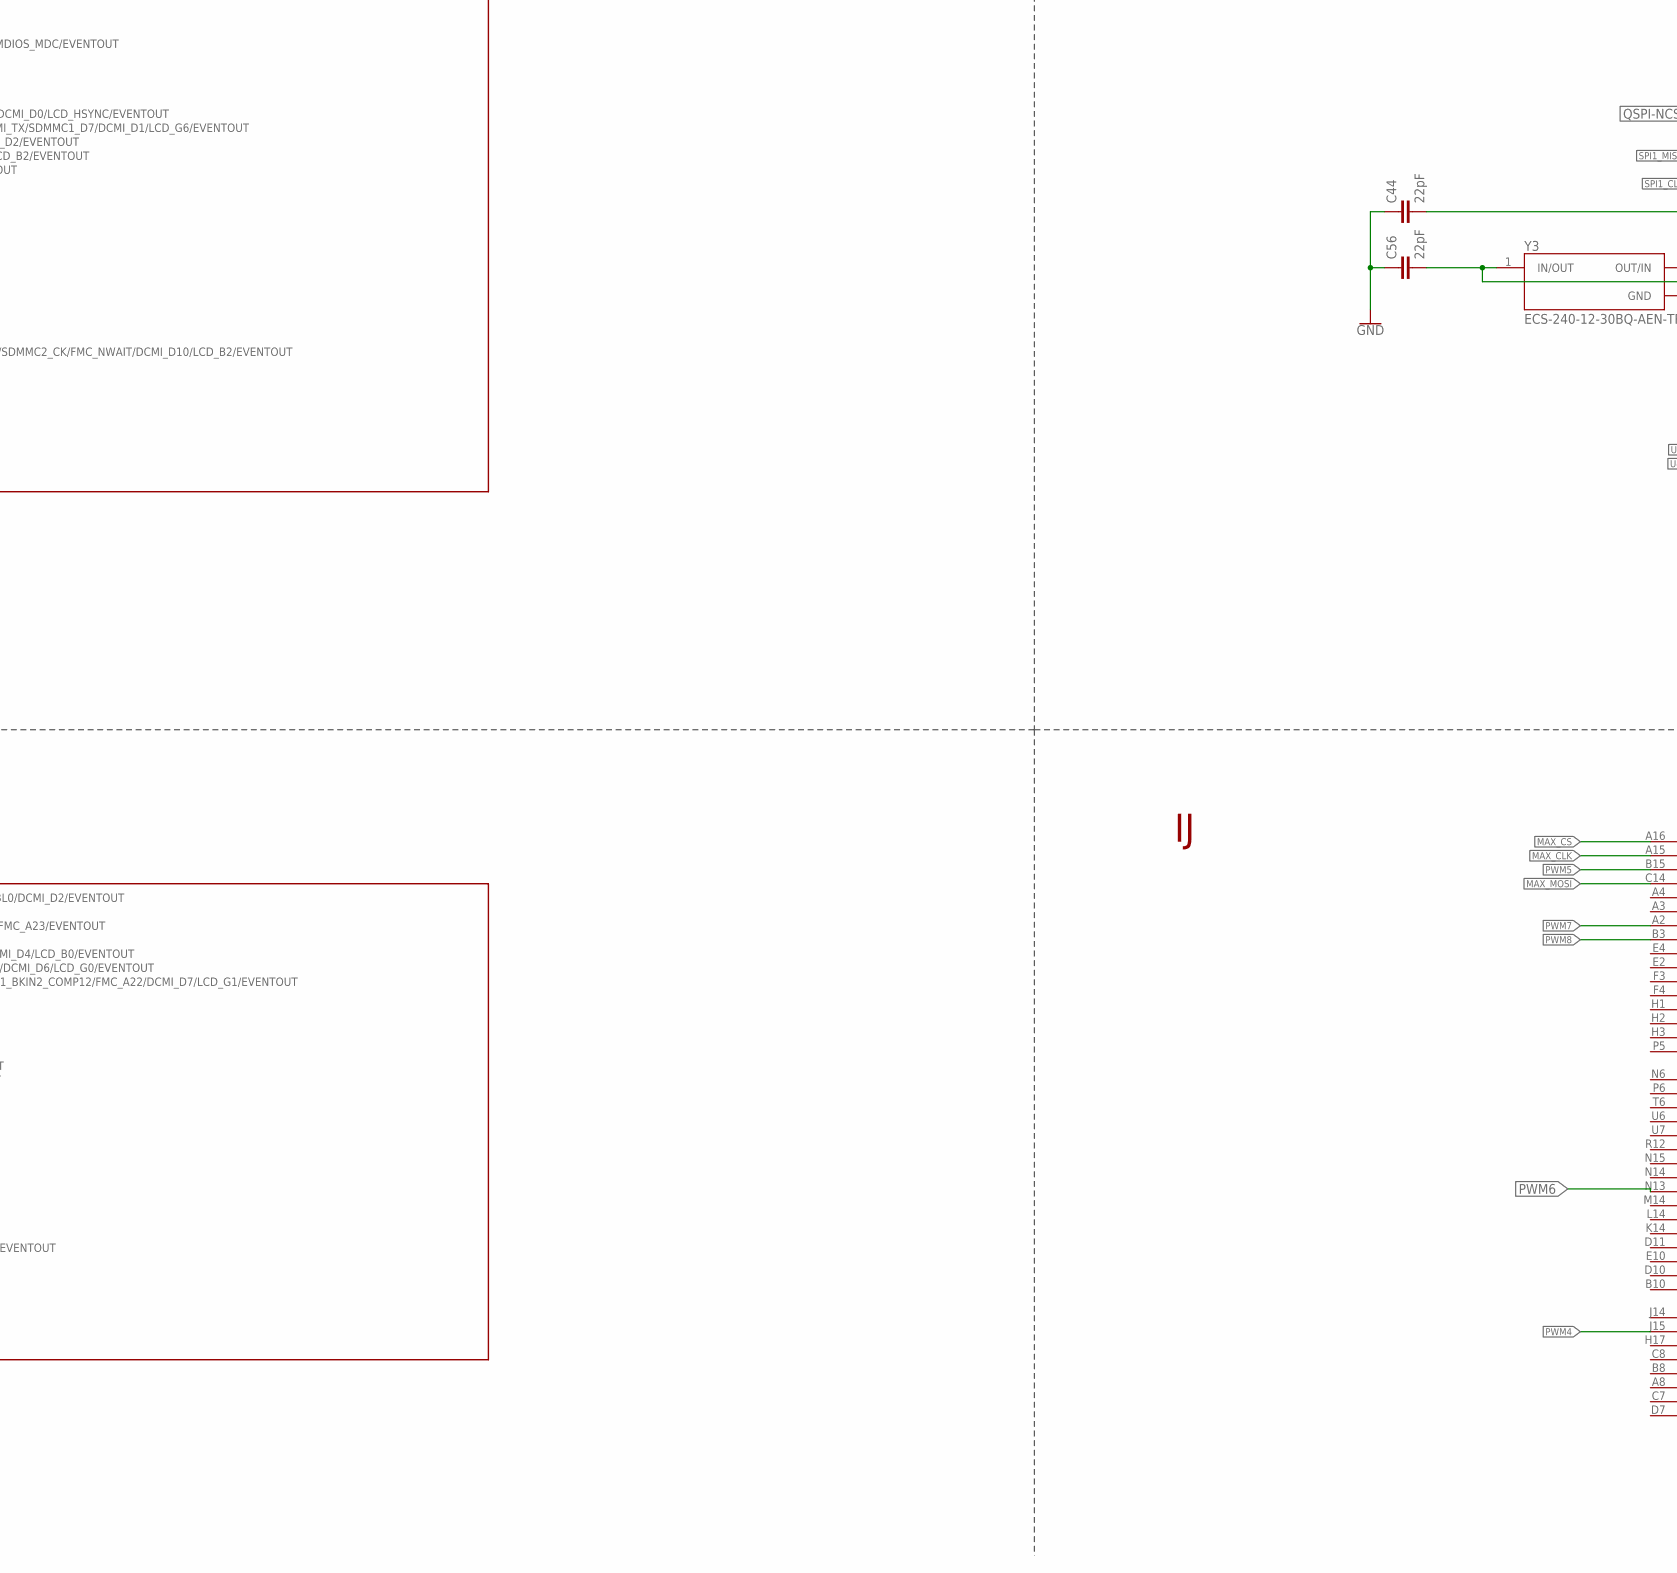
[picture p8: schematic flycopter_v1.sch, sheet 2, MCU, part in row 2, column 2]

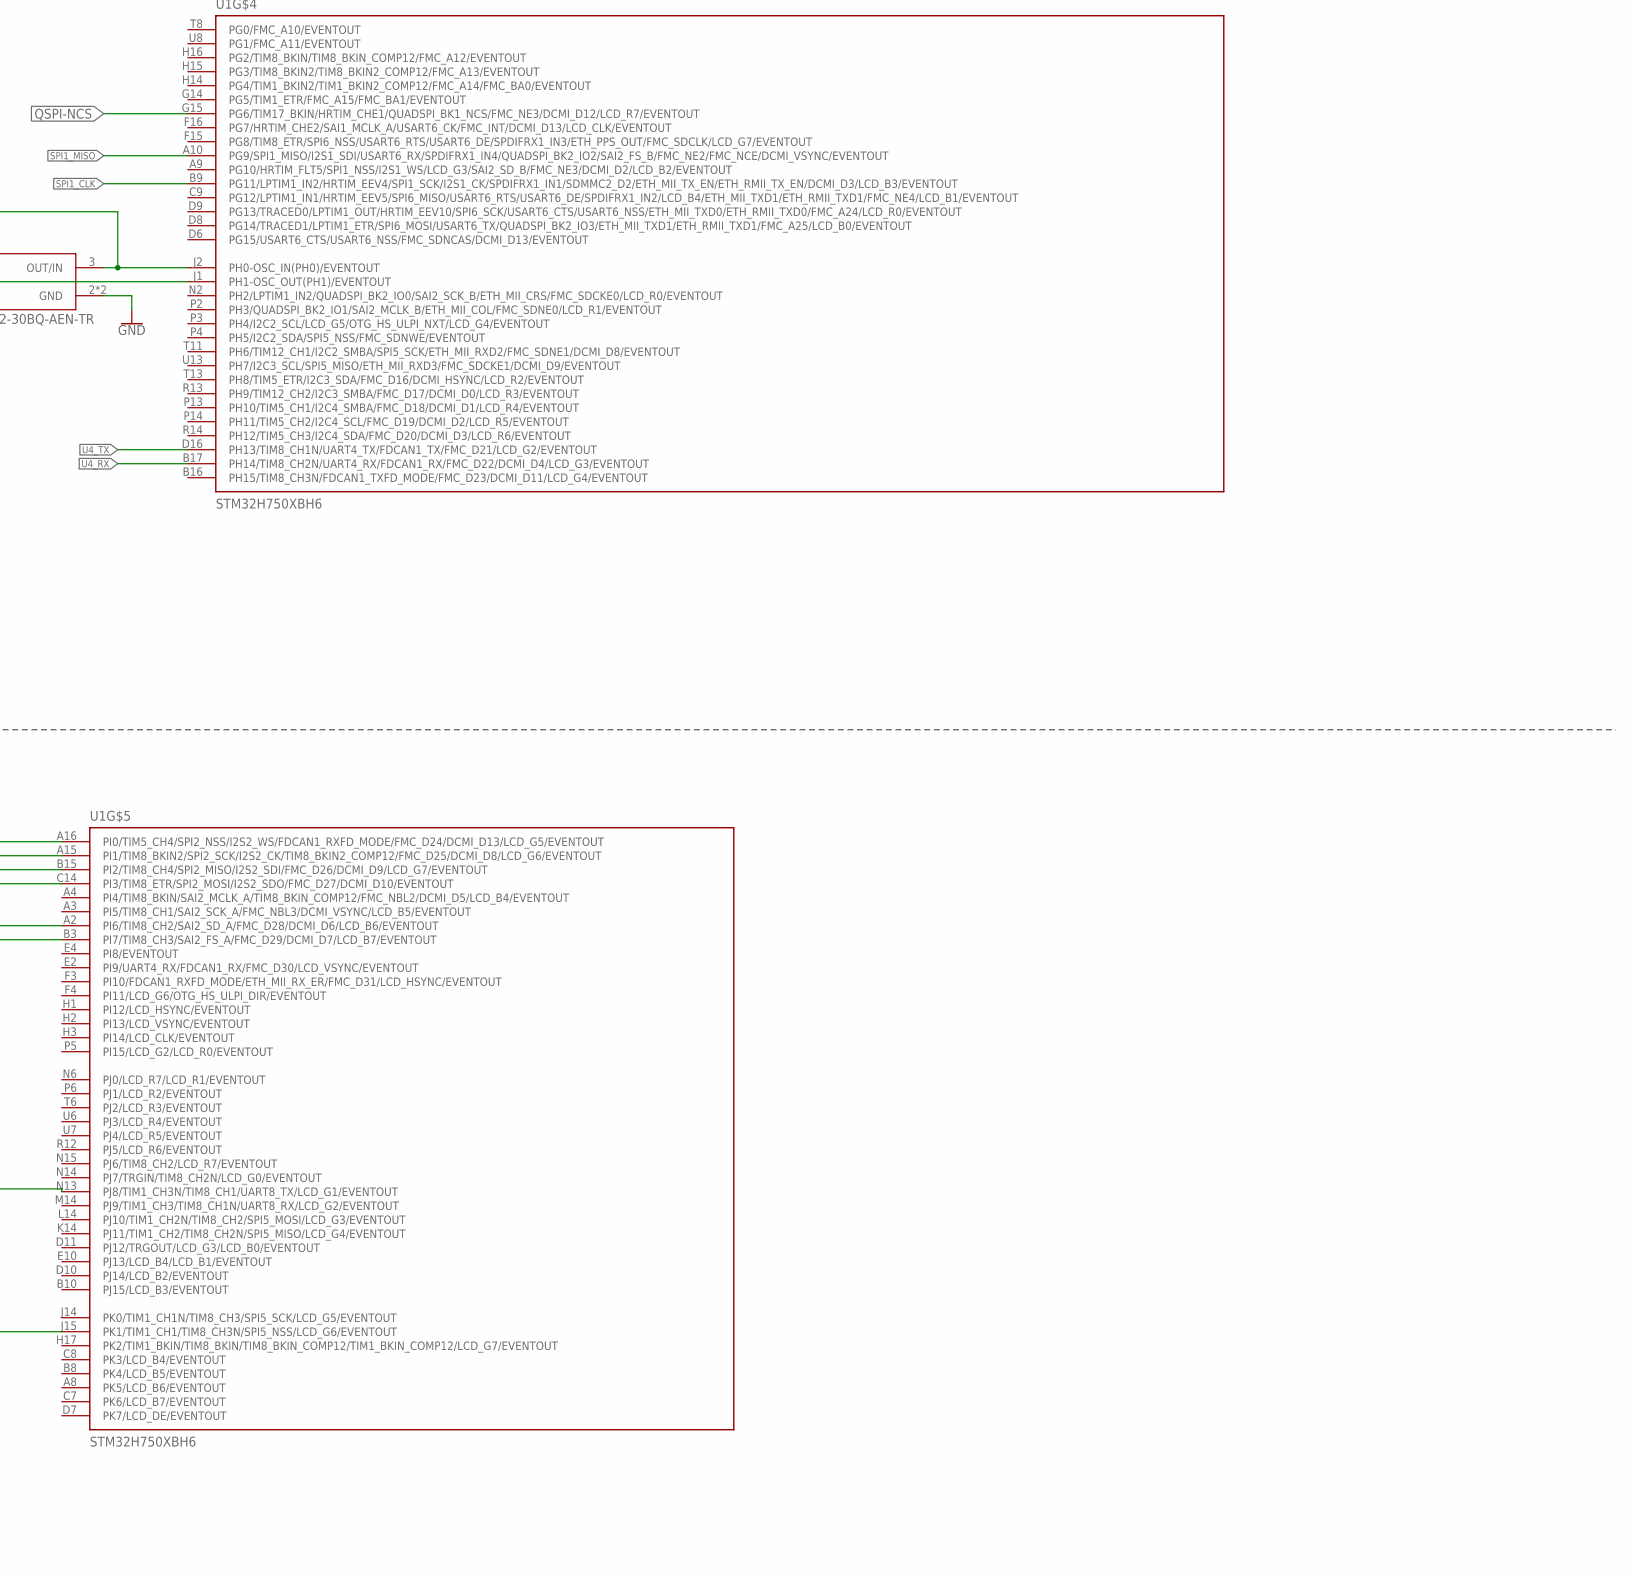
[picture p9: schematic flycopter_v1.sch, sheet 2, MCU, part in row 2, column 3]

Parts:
C6, C30: 2.2uF; C0603K
C42: 100nF; C0603K
C44, C56: 22pF; C0402K
D1: BAS16J; DIODE_SOD123
DAC: TPTP06R; TP06R
R20, R22: 100k; R0402
SBOOT: TPTP06R; TP06R
SRST: TPTP06R; TP06R
U1: STM32H750XBH6; IC_STM32H750XBH6
Y3: ECS-240-12-30BQ-AEN-TR; XTAL_ECS-240-12-30BQ-AEN-TR

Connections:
3V3: D1.A, R22.1, U1.A6 (VDDLDO), U1.C17 (VDDLDO), U1.E6 (VDD_1), U1.E7 (PDR_ON), U1.E9 (VDD_1), U1.E11 (VDD_1), U1.F5 (VDD_1), U1.F17 (VDD33USB), U1.G5 (VDD_1), U1.G13 (VDD_1), U1.G17 (VDD50USB), U1.H5 (VDD_1), U1.H13 (VDD_1), U1.J13 (VDD_1), U1.K5 (VDD_2), U1.K13 (VDD_1), U1.L1 (VDDA), U1.L5 (VDD_2), U1.L13 (VDD_1), U1.M1 (VREF+), U1.M5 (VDD_2), U1.M13 (VDD_2), U1.N7 (VDD_2), U1.N8 (VDD_2), U1.N10 (VDD_2), U1.N11 (VDD_2), U1.N12 (VDD_2), U1.P17 (VDD_2), U1.U12 (VDDLDO); also elsewhere on the board
!CARD_DTC: U1.T1 (PA0_C/TIM2_CH1/TIM2_ETR/TIM5_CH1/TIM8_E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); also elsewhere on the board
BARO_SCL: U1.D5 (PB8/TIM16_CH1/TIM4_CH3/DFSDM1_CKIN7/I2C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); also elsewhere on the board
BARO_SDA: U1.D4 (PB9/TIM17_CH1/TIM4_CH4/DFSDM1_DATIN7/I2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); also elsewhere on the board
BOOT0: R20.1, SBOOT.TP, U1.E8 (BOOT0)
DAC1: DAC.TP, U1.U3 (PA4/D1PWREN/TIM5_ETR/SPI1_NSS/I2S1_WS/S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)
ESP_CLK: U1.A13 (PC10/HRTIM_EEV1/DFSDM1_CKIN5/SPI3_SCK/I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); also elsewhere on the board
ESP_CS: U1.E3 (PC13/EVENTOUT); also elsewhere on the board
ESP_MISO: U1.B13 (PC11/HRTIM_FLT2/DFSDM1_DATIN5/SPI3_MISO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); also elsewhere on the board
ESP_MOSI: U1.A5 (PB5/TIM17_BKIN/TIM3_CH2/HRTIM_EEV7/I2C1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); also elsewhere on the board
GND: C6.2, C30.2, C42.1, C44.1, C56.1, R20.2, U1.A1 (VSS_1), U1.A17 (VSS_1), U1.B2 (VSS_1), U1.B6 (VSS_1), U1.C10 (VSS_1), U1.C13 (VSS_1), U1.C16 (VSS_1), U1.F2 (VSS_1), U1.G7 (VSS_2), U1.G8 (VSS_2), U1.G9 (VSS_2), U1.G10 (VSS_2), U1.G11 (VSS_2), U1.G16 (VSS_2), U1.H7 (VSS_2), U1.H8 (VSS_2), U1.H9 (VSS_2), U1.H10 (VSS_2), U1.H11 (VSS_3), U1.J3 (VSS_1), U1.J7 (VSS_3), U1.J8 (VSS_3), U1.J9 (VSS_3), U1.J10 (VSS_3), U1.J11 (VSS_3), U1.J16 (VSS_1), U1.J17 (VSS_1), U1.K7 (VSS_3), U1.K8 (VSS_3), U1.K9 (VSS_3), U1.K10 (VSS_3), U1.K11 (VSS_3), U1.K15 (VSS_2), U1.L7 (VSS_3), U1.L8 (VSS_3), U1.L9 (VSS_3), U1.L10 (VSS_3), U1.L11 (VSS_3), U1.L15 (VSS_2), U1.M15 (VSS_2), U1.N1 (VREF-), U1.N16 (VSS_1), U1.P1 (VSSA), U1.R4 (VSS_1), U1.R8 (VSS_2), U1.T12 (VSS_1), U1.U1 (VSS_2), U1.U17 (VSS_1), Y3.2 (GND), Y3.4 (GND); also elsewhere on the board
I2C2_SCL: U1.G3 (PF1/I2C2_SCL/FMC_A1/EVENTOUT); also elsewhere on the board
I2C2_SDA: U1.G4 (PF0/I2C2_SDA/FMC_A0/EVENTOUT); also elsewhere on the board
IMU_SCL: U1.E15 (PA8/MCO1/TIM1_CH1/HRTIM_CHB2/TIM8_BKIN2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); also elsewhere on the board
IMU_SDA: U1.E14 (PC9/MCO2/TIM3_CH4/TIM8_CH4/I2C3_SDA/I2S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); also elsewhere on the board
J-SWD-CLK: U1.B14 (PA14/JTCK-SWCLK/EVENTOUT); also elsewhere on the board
J-SWD-IO: U1.C15 (PA13/JTMS-SWDIO/EVENTOUT); also elsewhere on the board
LED_STATUS: U1.U5 (PB0/TIM1_CH2N/TIM3_CH3/TIM8_CH2N/DFSDM1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); also elsewhere on the board
LED_STATUS2: U1.L2 (PC0/DFSDM1_CKIN0/DFSDM1_DATIN4/SAI2_FS_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); also elsewhere on the board
MAX_CLK: U1.A15 (PI1/TIM8_BKIN2/SPI2_SCK/I2S2_CK/TIM8_BK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); also elsewhere on the board
MAX_CS: U1.A16 (PI0/TIM5_CH4/SPI2_NSS/I2S2_WS/FDCAN1_RX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); also elsewhere on the board
MAX_MISO: U1.M3 (PC2/CDSLEEP/DFSDM1_CKIN1/SPI2_MISO/I2S2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); also elsewhere on the board
MAX_MOSI: U1.C14 (PI3/TIM8_ETR/SPI2_MOSI/I2S2_SDO/FMC_D27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); also elsewhere on the board
MMC_!CS: U1.B7 (PB4/NJTRST/TIM16_BKIN/TIM3_CH1/HRTIM_EE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); also elsewhere on the board
MMC_CLK: U1.M2 (PC1/TRACED0/SAI1_D1/DFSDM1_DATIN0/DFSDM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); also elsewhere on the board
MMC_CMD: U1.N5 (PA0/TIM2_CH1/TIM2_ETR/TIM5_CH1/TIM8_ETR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); also elsewhere on the board
MMC_D0: U1.U15 (PB14/TIM1_CH2N/TIM12_CH1/TIM8_CH2N/USAR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); also elsewhere on the board
MMC_D1: U1.T15 (PB15/RTC_REFIN/TIM1_CH3N/TIM12_CH2/TIM8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); also elsewhere on the board
MMC_D2: U1.C6 (PB3/JTDO/TRACESWO/TIM2_CH2/HRTIM_FLT4/S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); also elsewhere on the board
MT1: U1.T5 (PB1/TIM1_CH3N/TIM3_CH4/TIM8_CH3N/DFSDM1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); also elsewhere on the board
MT2: U1.F14 (PC6/HRTIM_CHA1/TIM3_CH1/TIM8_CH1/DFSDM1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); also elsewhere on the board
MT3: U1.F13 (PC7/TRGIO/HRTIM_CHA2/TIM3_CH2/TIM8_CH2/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); also elsewhere on the board
MT4: U1.E13 (PC8/TRACED1/HRTIM_CHB1/TIM3_CH3/TIM8_CH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); also elsewhere on the board
MT5: U1.N4 (PA1/TIM2_CH2/TIM5_CH2/LPTIM3_OUT/TIM15_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); also elsewhere on the board
MT6: U1.N3 (PA2/TIM2_CH3/TIM5_CH3/LPTIM4_OUT/TIM15_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); also elsewhere on the board
MT7: U1.T3 (PA5/D2PWREN/TIM2_CH1/TIM2_ETR/TIM8_CH1N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); also elsewhere on the board
MT8: U1.P12 (PB11/TIM2_CH4/HRTIM_SCIN/LPTIM2_ETR/I2C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); also elsewhere on the board
unnamed: C42.2, R22.2, SRST.TP, U1.K1 (NRST)
unnamed: D1.C, U1.B1 (VBAT)
unnamed: C6.1, U1.A7 (VCAP), U1.D17 (VCAP), U1.U11 (VCAP)
unnamed: C44.2, U1.J2 (PH0-OSC_IN(PH0)/EVENTOUT), Y3.3 (OUT/IN)
unnamed: C56.2, U1.J1 (PH1-OSC_OUT(PH1)/EVENTOUT), Y3.1 (IN/OUT)
PWM1: U1.D15 (PA9/TIM1_CH2/HRTIM_CHC1/LPUART1_TX/I2C3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); also elsewhere on the board
PWM2: U1.D14 (PA10/TIM1_CH3/HRTIM_CHC2/LPUART1_RX/USA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); also elsewhere on the board
PWM3: U1.U10 (PE14/TIM1_CH4/SPI4_MOSI/SAI2_MCLK_B/FMC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); also elsewhere on the board
PWM4: U1.J15 (PK1/TIM1_CH1/TIM8_CH3N/SPI5_NSS/LCD_G6/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); also elsewhere on the board
PWM5: U1.B15 (PI2/TIM8_CH4/SPI2_MISO/I2S2_SDI/FMC_D26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); also elsewhere on the board
PWM6: U1.N13 (PJ8/TIM1_CH3N/TIM8_CH1/UART8_TX/LCD_G1/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); also elsewhere on the board
PWM7: U1.A2 (PI6/TIM8_CH2/SAI2_SD_A/FMC_D28/DCMI_D6/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); also elsewhere on the board
PWM8: U1.B3 (PI7/TIM8_CH3/SAI2_FS_A/FMC_D29/DCMI_D7/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); also elsewhere on the board
QSPI-!HOLD: U1.K2 (PF6/TIM16_CH1/SPI5_NSS/SAI1_SD_B/UART7_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); also elsewhere on the board
QSPI-!WP: U1.C3 (PE2/TRACECLK/SAI1_CK1/SPI4_SCK/SAI1_MCL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); also elsewhere on the board
QSPI-CLK: U1.R6 (PB2/RTC_OUT/SAI1_D1/DFSDM1_CKIN1/SAI1_S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); also elsewhere on the board
QSPI-MISO: U1.K4 (PF8/TIM16_CH1N/SPI5_MISO/SAI1_SCK_B/UAR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); also elsewhere on the board
QSPI-MOSI: U1.L4 (PF9/TIM17_CH1N/SPI5_MOSI/SAI1_FS_B/UART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); also elsewhere on the board
QSPI-NCS: U1.G15 (PG6/TIM17_BKIN/HRTIM_CHE1/QUADSPI_BK1_N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); also elsewhere on the board
SBUS_RX: U1.R16 (PD12/LPTIM1_IN1/TIM4_CH1/LPTIM2_IN1/I2C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), U1.T14 (PB12/TIM1_BKIN/I2C2_SMBA/SPI2_NSS/I2S2_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); also elsewhere on the board
SPI1_CLK: U1.B9 (PG11/LPTIM1_IN2/HRTIM_EEV4/SPI1_SCK/I2S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)
SPI1_MISO: U1.A10 (PG9/SPI1_MISO/I2S1_SDI/USART6_RX/SPDIFR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)
SPI1_MOSI: U1.C11 (PD7/DFSDM1_DATIN4/SPI1_MOSI/I2S1_SDO/DF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)
U1_RX: U1.C5 (PB7/TIM17_CH1N/TIM4_CH2/HRTIM_EEV9/I2C1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); also elsewhere on the board
U1_TX: U1.B5 (PB6/TIM16_CH1N/TIM4_CH1/HRTIM_EEV8/I2C1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); also elsewhere on the board
U2_RX: U1.B11 (PD6/SAI1_D1/DFSDM1_CKIN4/DFSDM1_DATIN1/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)
U2_TX: U1.A11 (PD5/HRTIM_EEV3/USART2_TX/FDCAN1_TXFD_MO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)
U3_RX: U1.T17 (PD9/DFSDM1_DATIN3/SAI3_SD_B/USART3_RX/F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); also elsewhere on the board
U3_TX: U1.P11 (PB10/TIM2_CH3/HRTIM_SCOUT/LPTIM2_IN1/I2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); also elsewhere on the board
U4_RX: U1.B17 (PH14/TIM8_CH2N/UART4_RX/FDCAN1_RX/FMC_D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); also elsewhere on the board
U4_TX: U1.D16 (PH13/TIM8_CH1N/UART4_TX/FDCAN1_TX/FMC_D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); also elsewhere on the board
U5_RX: U1.D12 (PD2/TRACED2/TIM3_ETR/UART5_RX/SDMMC1_CM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); also elsewhere on the board
U5_TX: U1.C12 (PC12/TRACED3/HRTIM_EEV2/SPI3_MOSI/I2S3_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); also elsewhere on the board
USB_D_N: U1.E17 (PA11/TIM1_CH4/HRTIM_CHD1/LPUART1_CTS/SP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); also elsewhere on the board
USB_D_P: U1.E16 (PA12/TIM1_ETR/HRTIM_CHD2/LPUART1_RTS/LP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); also elsewhere on the board
VBAT_BUFF: U1.T7 (PF11/SPI5_MOSI/SAI2_SD_B/FMC_SDNRAS/DCM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); also elsewhere on the board

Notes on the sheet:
6 x UART 2 x I2C (BARO, IMU) 4 x SPI (ESP, MAX74x, MMC, ) 8 x TIM(MOTOR OUT) 1 x SBUS 8 x RC IN
ARM-7 STM32 H7

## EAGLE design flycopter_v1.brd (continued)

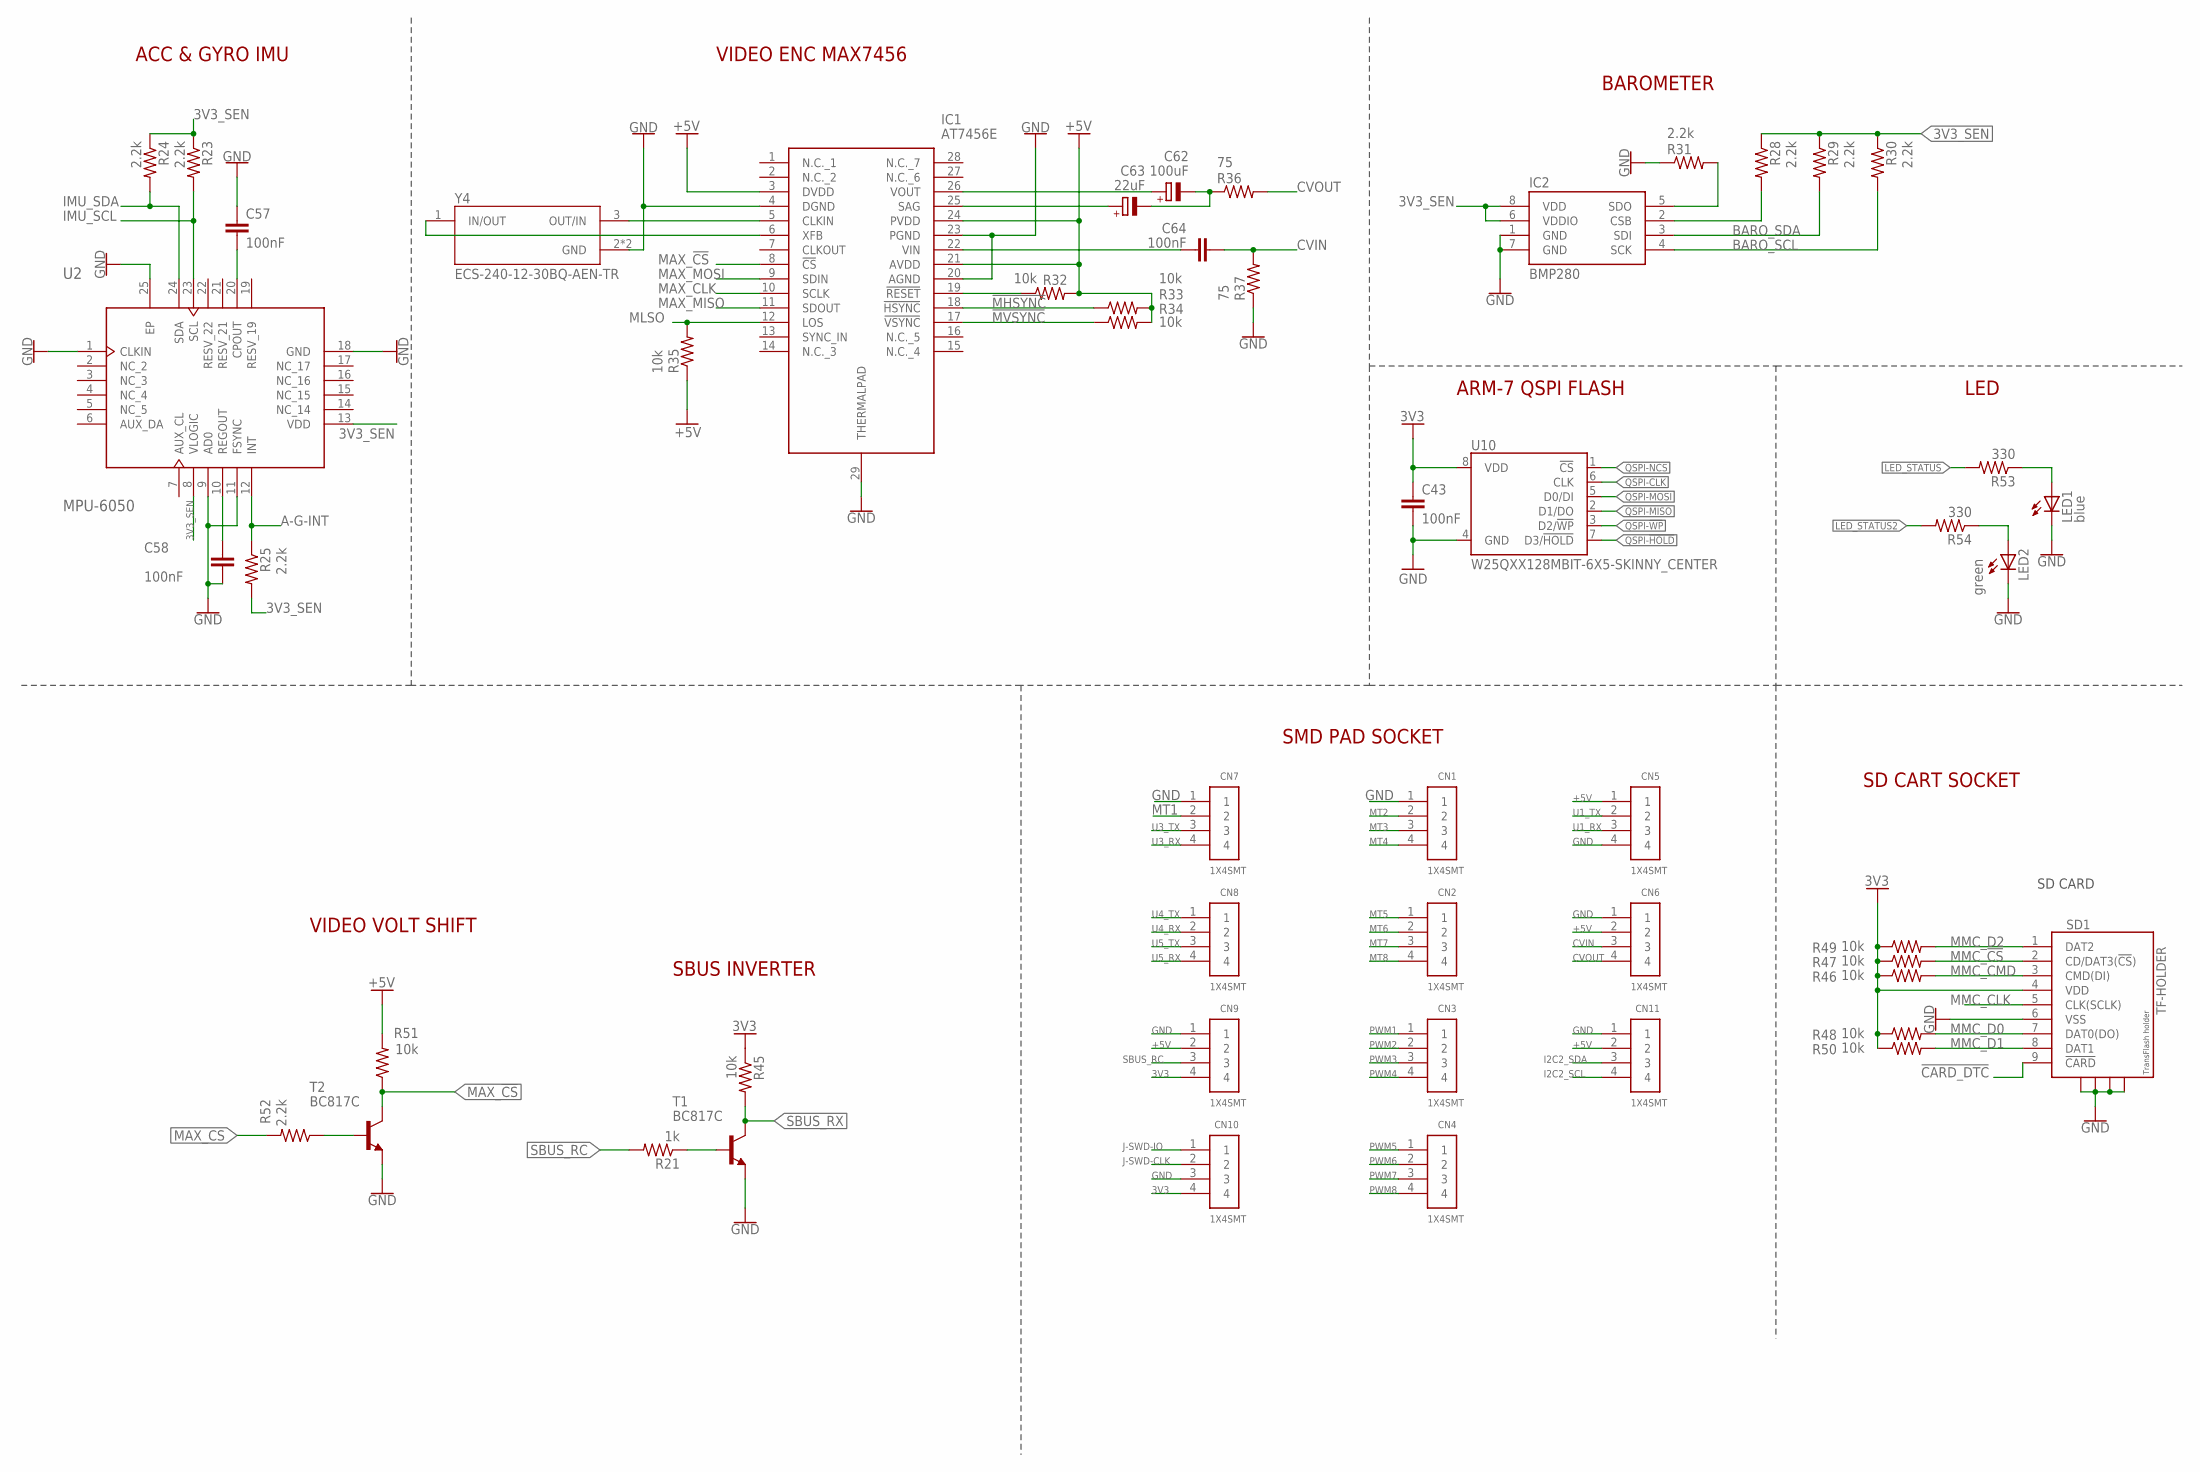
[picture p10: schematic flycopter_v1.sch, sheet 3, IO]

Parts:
C43, C57, C58, C64: 100nF; C0603K
C62: 100uF; A/3216-18R
C63: 22uF; A/3216-18R
CN1, CN2, CN3, CN4, CN5, CN6, CN7, CN8, CN9, CN10, CN11: 1X4SMT; 1X4-SMT
IC1: AT7456E; SOP65P640X120-29N
IC2: BMP280
LED1: blue; CHIPLED_0603
LED2: green; CHIPLED_0603
R21: 1k; R0402
R23, R24, R25, R28, R29, R30, R31, R52: 2.2k; R0402
R32, R33, R34, R35, R45, R46, R47, R48, R49, R50, R51: 10k; R0402
R36, R37: 75; R0402
R53, R54: 330; R0402
SD1: TF-HOLDER; TF-PULL
T1, T2: BC817C; SOT23-BEC
U2: MPU-6050; 24-VFQFN
U10: W25QXX128MBIT-6X5-SKINNY_CENTER; WSON-8-6X5-SKINNY_CENTERPAD
Y4: ECS-240-12-30BQ-AEN-TR; XTAL_ECS-240-12-30BQ-AEN-TR

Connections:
3V3: C43.1, CN9.4, CN10.4, R45.1, R46.1, R47.1, R48.1, R49.1, R50.1, SD1.4 (VDD), U10.8 (VDD); also elsewhere on the board
3V3_SEN: IC2.6 (VDDIO), IC2.8 (VDD), R23.1, R24.1, R25.2, R28.1, R29.1, R30.1, U2.8 (VLOGIC), U2.13 (VDD); also elsewhere on the board
!CARD_DTC: SD1.9 (!CARD); also elsewhere on the board
!MHSYNC: IC1.18 (!HSYNC), R33.1
!MVSYNC: IC1.17 (!VSYNC), R34.1
+5V: CN5.1, CN6.2, CN9.2, CN11.2, IC1.3 (DVDD), IC1.21 (AVDD), IC1.24 (PVDD), R32.2, R33.2, R34.2, R35.1, R51.2; also elsewhere on the board
A-G-INT: R25.1, U2.12 (INT)
BARO_SCL: IC2.4 (SCK), R30.2; also elsewhere on the board
BARO_SDA: IC2.3 (SDI), R29.2; also elsewhere on the board
CVIN: C64.2, CN6.3, R37.2
CVOUT: CN6.4, R36.2
GND: C43.2, C57.1, C58.2, CN1.1, CN5.4, CN6.1, CN7.1, CN9.1, CN10.3, CN11.1, IC1.4 (DGND), IC1.20 (AGND), IC1.23 (PGND), IC1.29 (THERMALPAD), IC2.1 (GND), IC2.7 (GND), LED1.C, LED2.C, R31.1, R37.1, SD1.6 (VSS), SD1.S1, SD1.S2, SD1.S3, SD1.S4, T1.E, T2.E, U2.1 (CLKIN), U2.9 (AD0), U2.11 (FSYNC), U2.18 (GND), U2.25 (EP), U10.4 (GND), Y4.2 (GND), Y4.4 (GND); also elsewhere on the board
I2C2_SCL: CN11.4; also elsewhere on the board
I2C2_SDA: CN11.3; also elsewhere on the board
IMU_SCL: R23.2, U2.23 (SCL); also elsewhere on the board
IMU_SDA: R24.2, U2.24 (SDA); also elsewhere on the board
J-SWD-CLK: CN10.2; also elsewhere on the board
J-SWD-IO: CN10.1; also elsewhere on the board
LED_STATUS: R53.2; also elsewhere on the board
LED_STATUS2: R54.2; also elsewhere on the board
MAX_!CS: IC1.8 (!CS), R51.1, T2.C
MAX_CLK: IC1.10 (SCLK); also elsewhere on the board
MAX_CS: R52.2; also elsewhere on the board
MAX_MISO: IC1.11 (SDOUT); also elsewhere on the board
MAX_MOSI: IC1.9 (SDIN); also elsewhere on the board
MLSO: IC1.12 (LOS), R35.2
MMC_!CS: R47.2, SD1.2 (CD/DAT3(!CS!)); also elsewhere on the board
MMC_CLK: SD1.5 (CLK(SCLK)); also elsewhere on the board
MMC_CMD: R46.2, SD1.3 (CMD(DI)); also elsewhere on the board
MMC_D0: R48.2, SD1.7 (DAT0(DO)); also elsewhere on the board
MMC_D1: R50.2, SD1.8 (DAT1); also elsewhere on the board
MMC_D2: R49.2, SD1.1 (DAT2); also elsewhere on the board
MT1: CN7.2; also elsewhere on the board
MT2: CN1.2; also elsewhere on the board
MT3: CN1.3; also elsewhere on the board
MT4: CN1.4; also elsewhere on the board
MT5: CN2.1; also elsewhere on the board
MT6: CN2.2; also elsewhere on the board
MT7: CN2.3; also elsewhere on the board
MT8: CN2.4; also elsewhere on the board
unnamed: R21.1, T1.B
unnamed: LED1.A, R53.1
unnamed: LED2.A, R54.1
unnamed: R52.1, T2.B
unnamed: IC1.19 (!RESET), R32.1
unnamed: C57.2, U2.20 (CPOUT)
unnamed: C58.1, U2.10 (REGOUT)
unnamed: C62.+, IC1.26 (VOUT)
unnamed: IC2.2 (CSB), R28.2
unnamed: IC2.5 (SDO), R31.2
unnamed: C63.+, IC1.25 (SAG)
unnamed: C62.-, C63.-, R36.1
unnamed: C64.1, IC1.22 (VIN)
unnamed: IC1.6 (XFB), Y4.1 (IN/OUT)
unnamed: IC1.5 (CLKIN), Y4.3 (OUT/IN)
PWM1: CN3.1; also elsewhere on the board
PWM2: CN3.2; also elsewhere on the board
PWM3: CN3.3; also elsewhere on the board
PWM4: CN3.4; also elsewhere on the board
PWM5: CN4.1; also elsewhere on the board
PWM6: CN4.2; also elsewhere on the board
PWM7: CN4.3; also elsewhere on the board
PWM8: CN4.4; also elsewhere on the board
QSPI-!HOLD: U10.7 (D3/!HOLD!); also elsewhere on the board
QSPI-!WP: U10.3 (D2/!WP!); also elsewhere on the board
QSPI-CLK: U10.6 (CLK); also elsewhere on the board
QSPI-MISO: U10.2 (D1/DO); also elsewhere on the board
QSPI-MOSI: U10.5 (D0/DI); also elsewhere on the board
QSPI-NCS: U10.1 (!CS!); also elsewhere on the board
SBUS_RC: CN9.3, R21.2
SBUS_RX: R45.2, T1.C; also elsewhere on the board
U1_RX: CN5.3; also elsewhere on the board
U1_TX: CN5.2; also elsewhere on the board
U3_RX: CN7.4; also elsewhere on the board
U3_TX: CN7.3; also elsewhere on the board
U4_RX: CN8.2; also elsewhere on the board
U4_TX: CN8.1; also elsewhere on the board
U5_RX: CN8.4; also elsewhere on the board
U5_TX: CN8.3; also elsewhere on the board

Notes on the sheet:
ACC & GYRO IMU
VIDEO ENC MAX7456
BAROMETER
SD CARD
SBUS INVERTER
SD CART SOCKET
ARM-7 QSPI FLASH
LED
VIDEO VOLT SHIFT
SMD PAD SOCKET

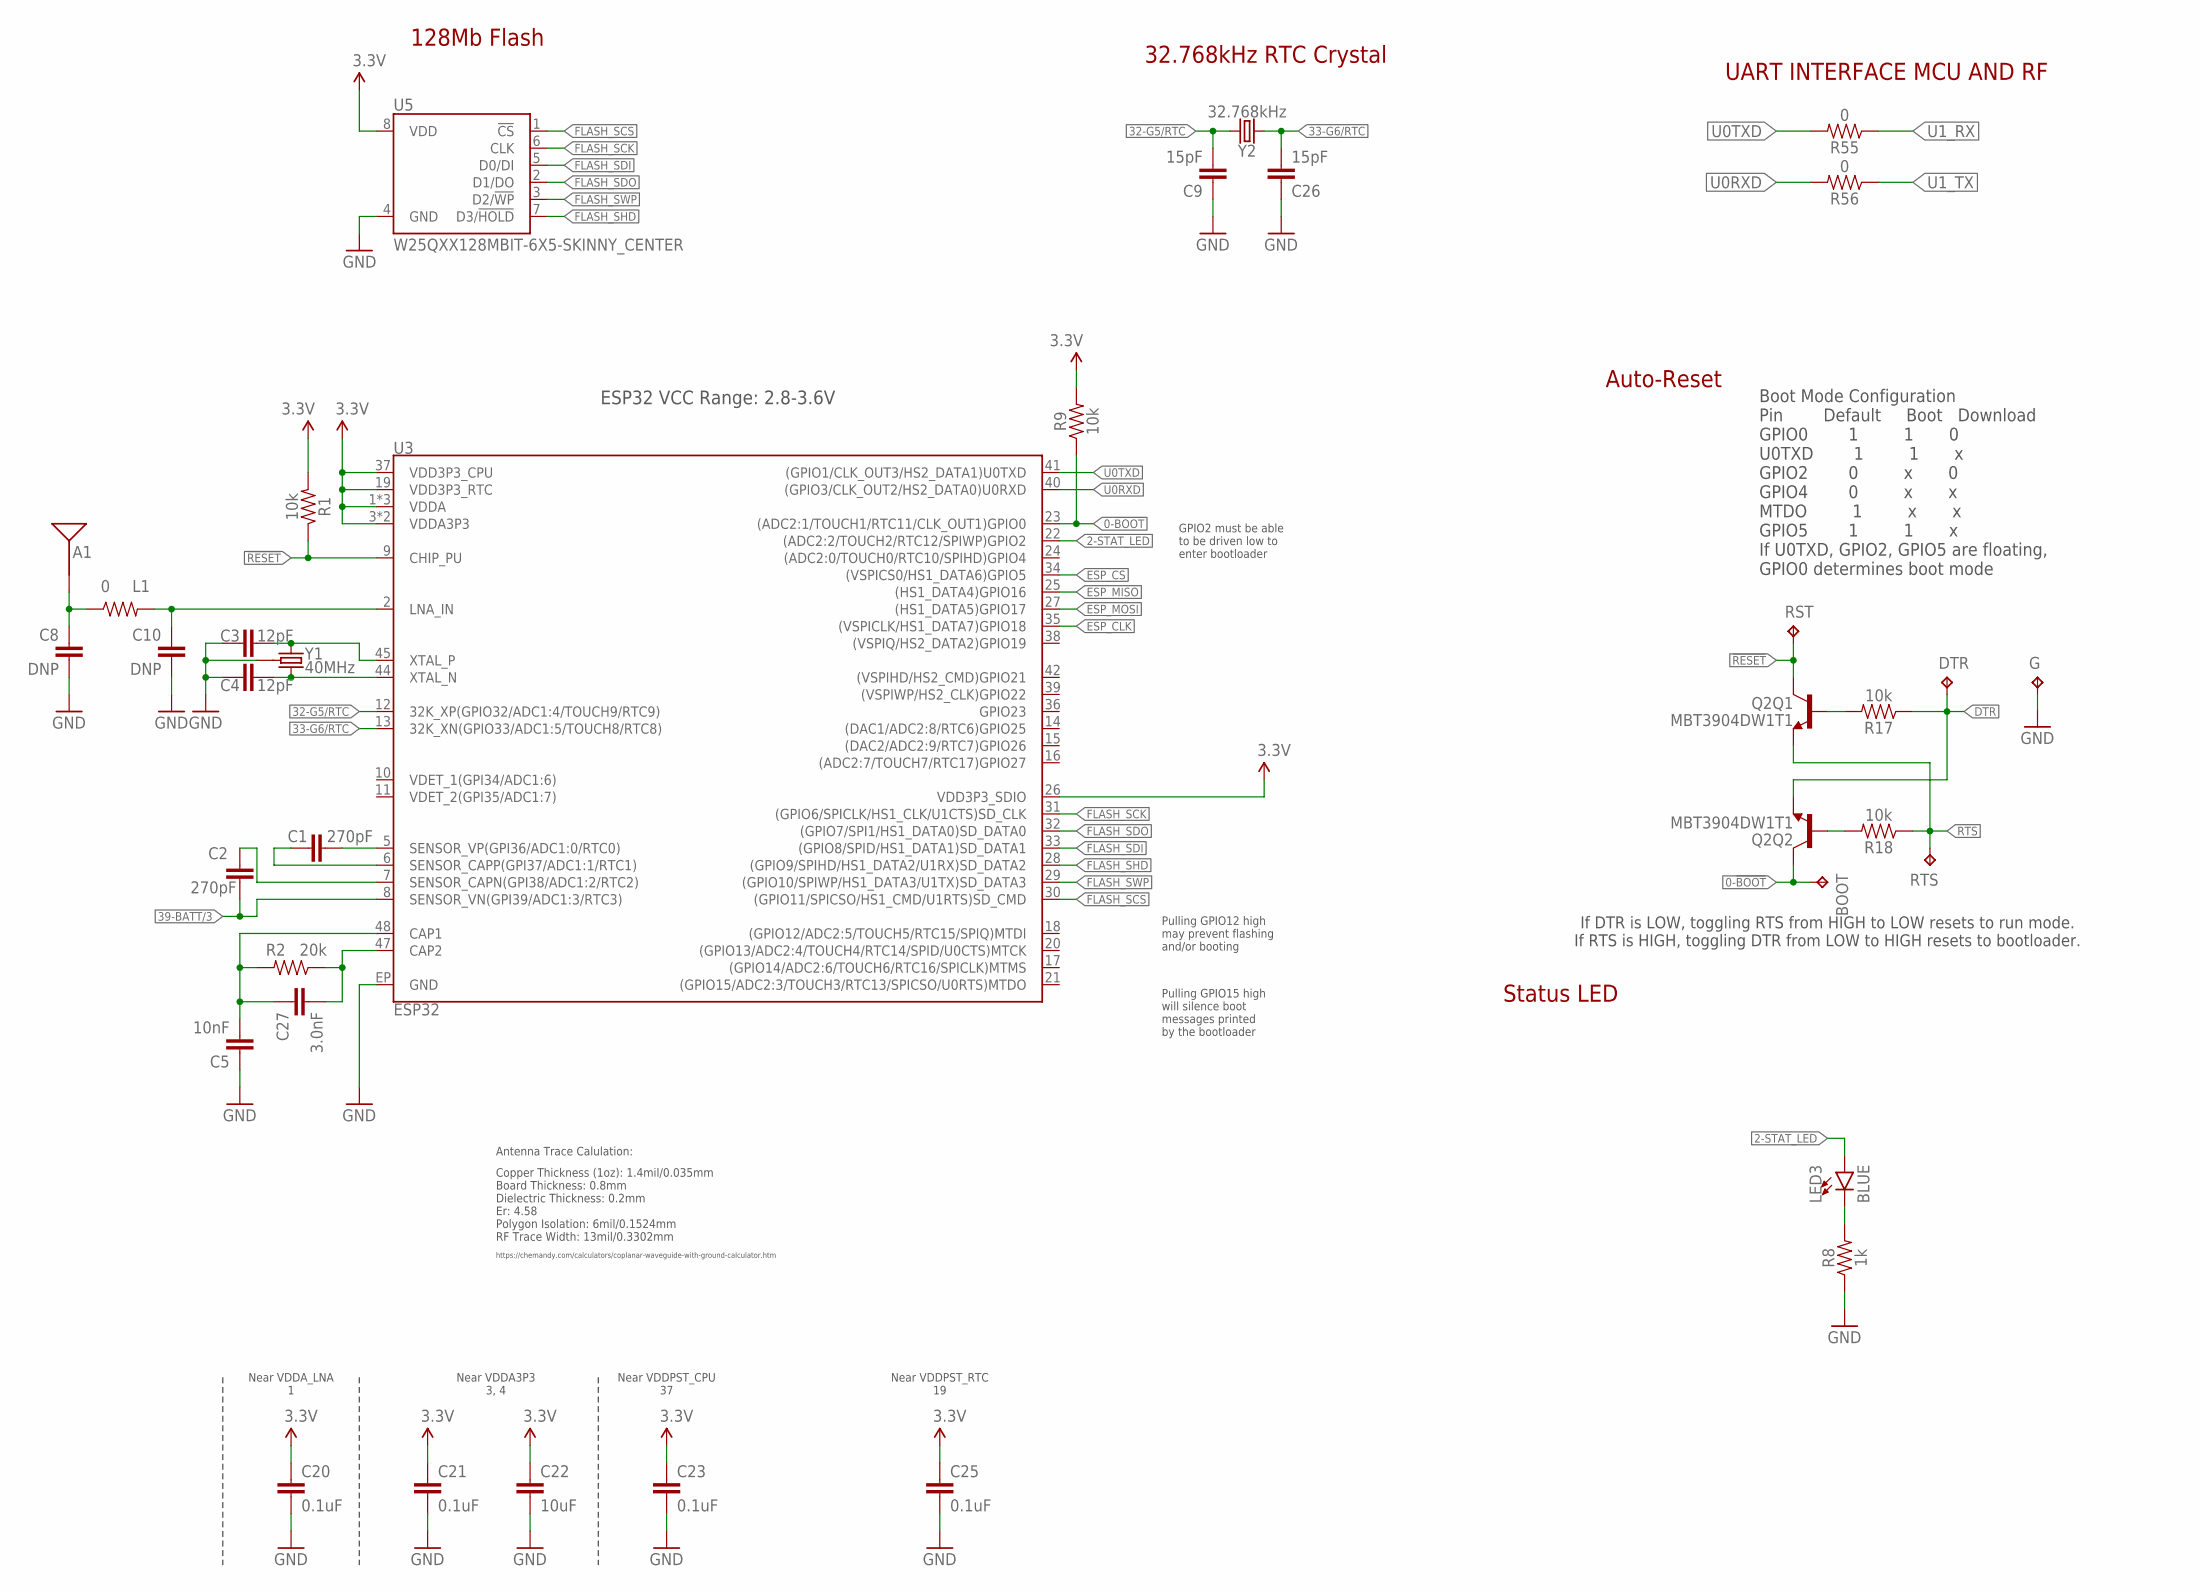
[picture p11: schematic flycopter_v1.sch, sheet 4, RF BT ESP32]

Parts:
A1: ANTENNA2.4GHZ-8.0X1.0MM; ANT-2.4GHZ-8.0X1.0MM
BOOT: TPTP06R; TP06R
C1, C2: 270pF; 0402-TIGHT
C3, C4: 12pF; 0402-TIGHT
C5: 10nF; 0402-TIGHT
C8, C10: DNP; 0402-TIGHT
C9, C26: 15pF; 0402-TIGHT
C20, C21, C23, C25: 0.1uF; 0402-TIGHT
C22: 10uF; 0402-TIGHT
C27: 3.0nF; 0402-TIGHT
DTR: TPTP06R; TP06R
G: TPTP06R; TP06R
L1: 0; 0402-TIGHT
LED3: BLUE; LED-0603
Q2: MBT3904DW1T1; SC70-6
R1, R9, R17, R18: 10k; 0402-TIGHT
R2: 20k; 0402-TIGHT
R8: 1k; 0402-TIGHT
R55, R56: 0; 0402-TIGHT
RST: TPTP06R; TP06R
RTS: TPTP06R; TP06R
U3: ESP32; QFN48-0.4MM
U5: W25QXX128MBIT-6X5-SKINNY_CENTER; WSON-8-6X5-SKINNY_CENTERPAD
Y1: 40MHz; CRYSTAL-SMD-2X2.5MM
Y2: 32.768kHz; CRYSTAL-SMD-3.2X1.5MM

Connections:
0-!BOOT!: BOOT.TP, Q2.6 (C), R9.1, U3.23 ((ADC2:1/TOUCH1/RTC11/CLK_OUT1)GPIO0)
2-STAT_LED: LED3.A, U3.22 ((ADC2:2/TOUCH2/RTC12/SPIWP)GPIO2)
3.3V: C20.1, C21.1, C22.1, C23.1, C25.1, R1.2, R9.2, U3.1 (VDDA), U3.3 (VDDA3P3), U3.4 (VDDA3P3), U3.19 (VDD3P3_RTC), U3.26 (VDD3P3_SDIO), U3.37 (VDD3P3_CPU), U3.43 (VDDA), U3.46 (VDDA), U5.8 (VDD); also elsewhere on the board
32-G5/RTC: C9.2, U3.12 (32K_XP(GPIO32/ADC1:4/TOUCH9/RTC9)), Y2.P$1 (1)
33-G6/RTC: C26.2, U3.13 (32K_XN(GPIO33/ADC1:5/TOUCH8/RTC8)), Y2.P$2 (2)
36: C1.2, U3.5 (SENSOR_VP(GPI36/ADC1:0/RTC0))
37: C1.1, U3.6 (SENSOR_CAPP(GPI37/ADC1:1/RTC1))
38: C2.1, U3.7 (SENSOR_CAPN(GPI38/ADC1:2/RTC2))
39-BATT/3: C2.2, U3.8 (SENSOR_VN(GPI39/ADC1:3/RTC3))
!RESET: Q2.3 (C), R1.1, RST.TP, U3.9 (CHIP_PU)
CAP_10N: C5.2, C27.1, R2.2, U3.48 (CAP1)
DTR: DTR.TP, Q2.1 (E), R17.1
ESP_CLK: U3.35 ((VSPICLK/HS1_DATA7)GPIO18); also elsewhere on the board
ESP_CS: U3.34 ((VSPICS0/HS1_DATA6)GPIO5); also elsewhere on the board
ESP_MISO: U3.25 ((HS1_DATA4)GPIO16); also elsewhere on the board
ESP_MOSI: U3.27 ((HS1_DATA5)GPIO17); also elsewhere on the board
FLASH_SCK: U3.31 ((GPIO6/SPICLK/HS1_CLK/U1CTS)SD_CLK), U5.6 (CLK)
FLASH_SCS: U3.30 ((GPIO11/SPICSO/HS1_CMD/U1RTS)SD_CMD), U5.1 (!CS!)
FLASH_SDI: U3.33 ((GPIO8/SPID/HS1_DATA1)SD_DATA1), U5.5 (D0/DI)
FLASH_SDO: U3.32 ((GPIO7/SPI1/HS1_DATA0)SD_DATA0), U5.2 (D1/DO)
FLASH_SHD: U3.28 ((GPIO9/SPIHD/HS1_DATA2/U1RX)SD_DATA2), U5.7 (D3/!HOLD!)
FLASH_SWP: U3.29 ((GPIO10/SPIWP/HS1_DATA3/U1TX)SD_DATA3), U5.3 (D2/!WP!)
GND: C3.1, C4.1, C5.1, C8.2, C9.1, C10.2, C20.2, C21.2, C22.2, C23.2, C25.2, C26.1, G.TP, R8.1, U3.EP (GND), U5.4 (GND), Y1.P2 (GND), Y1.P4 (GND); also elsewhere on the board
unnamed: Q2.5 (B), R17.2
unnamed: Q2.2 (B), R18.2
unnamed: C3.2, U3.45 (XTAL_P), Y1.P1 (1)
unnamed: C4.2, U3.44 (XTAL_N), Y1.P3 (2)
unnamed: LED3.C, R8.2
unnamed: C27.2, R2.1, U3.47 (CAP2)
unnamed: A1.FEED, C8.1, L1.1
unnamed: C10.1, L1.2, U3.2 (LNA_IN)
RTS: Q2.4 (E), R18.1, RTS.TP
U0RXD: R56.2, U3.40 ((GPIO3/CLK_OUT2/HS2_DATA0)U0RXD)
U0TXD: R55.2, U3.41 ((GPIO1/CLK_OUT3/HS2_DATA1)U0TXD)
U1_RX: R55.1; also elsewhere on the board
U1_TX: R56.1; also elsewhere on the board

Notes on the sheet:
Boot Mode Configuration Pin Default Boot Download GPIO0 1 1 0 U0TXD 1 1 x GPIO2 0 x 0 GPIO4 0 x x MTDO 1 x x GPIO5 1 1 x If U0TXD, GPIO2, GPIO5 are floating, GPIO0 determines boot mode
Auto-Reset
Near VDDA_LNA 1
Near VDDA3P3 3, 4
Near VDDPST_CPU 37
Near VDDPST_RTC 19
128Mb Flash
32.768kHz RTC Crystal
ESP32 VCC Range: 2.8-3.6V
Antenna Trace Calulation:
Copper Thickness (1oz): 1.4mil/0.035mm Board Thickness: 0.8mm Dielectric Thickness: 0.2mm Er: 4.58 Polygon Isolation: 6mil/0.1524mm RF Trace Width: 13mil/0.3302mm
https://chemandy.com/calculators/coplanar-waveguide-with-ground-calculator.htm
GPIO2 must be able to be driven low to enter bootloader
Pulling GPIO12 high may prevent flashing and/or booting
Pulling GPIO15 high will silence boot messages printed by the bootloader
UART INTERFACE MCU AND RF
Status LED
If DTR is LOW, toggling RTS from HIGH to LOW resets to run mode. If RTS is HIGH, toggling DTR from LOW to HIGH resets to bootloader.

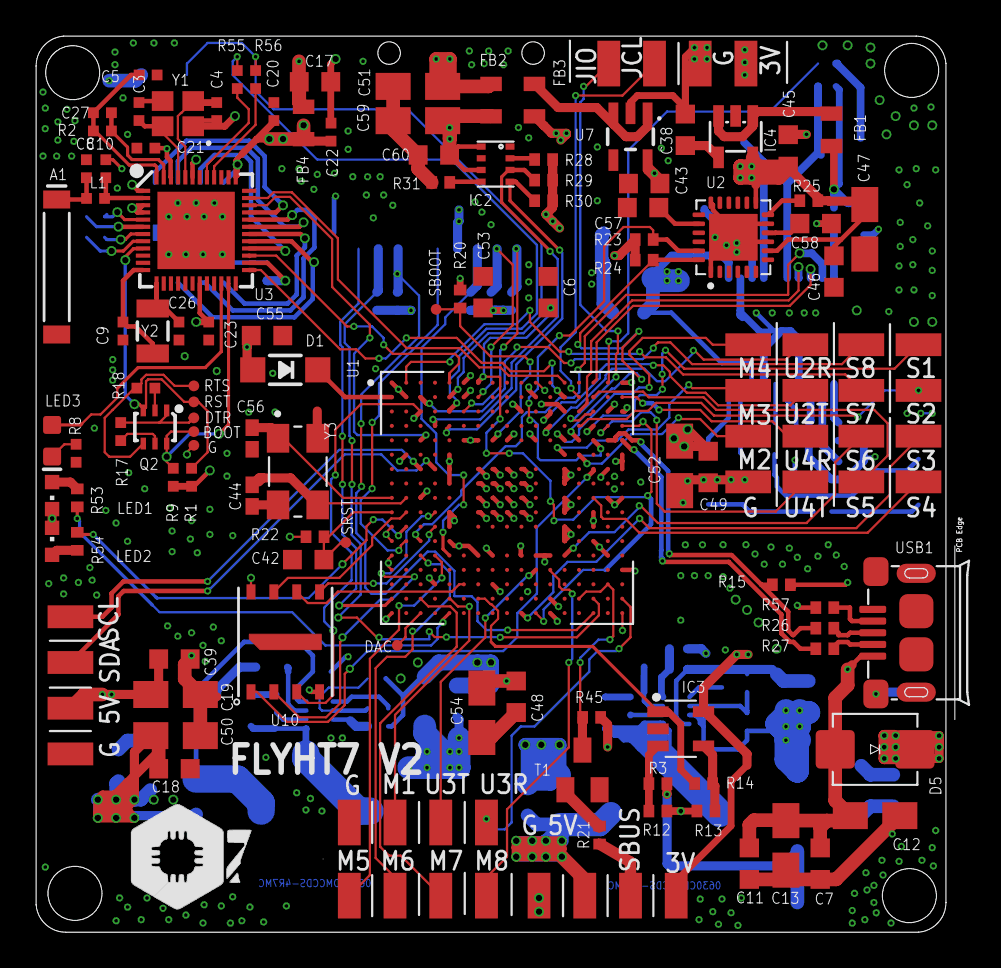
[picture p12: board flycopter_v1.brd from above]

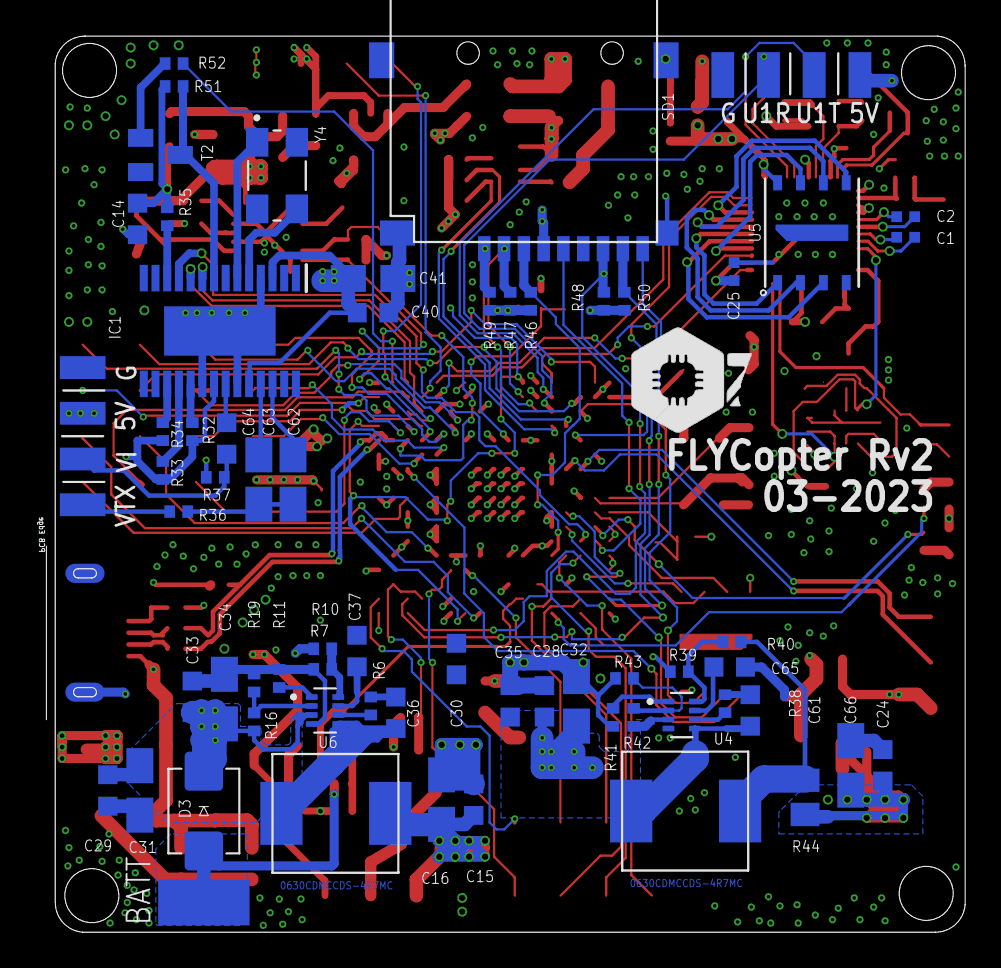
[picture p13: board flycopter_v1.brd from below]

Board: 4 copper layers, 50.5 x 49.8 mm, 178 parts (65 on the bottom side), 148 nets.

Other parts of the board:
U$1, U$2: OZK_20

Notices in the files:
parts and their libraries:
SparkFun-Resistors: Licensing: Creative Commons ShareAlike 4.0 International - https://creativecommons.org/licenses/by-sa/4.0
